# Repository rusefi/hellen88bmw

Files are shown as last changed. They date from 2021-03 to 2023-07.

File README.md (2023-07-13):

# Team

Product Owner @StefanSt

[Issue Tracker](https://github.com/rusefi/hellen88bmw-issues)

[User documentation](https://rusefi.com/s/hellen88bmw)

Part of https://github.com/andreika-git/hellen-one family

Inspired by https://github.com/rusefi/hw_88_bmw

# compatible cases

0260002360 TCU yes or no?

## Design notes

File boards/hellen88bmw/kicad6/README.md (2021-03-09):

Part of https://github.com/andreika-git/hellen-one family

https://docs.google.com/spreadsheets/d/1OiEaak7TElKwF-fXWvl9Dk-fD84a0NENe6lOwhXiOe4/

Inspired by https://github.com/rusefi/hw_88_bmw

https://github.com/rusefi/hw_microRusEfi

We shall start from https://github.com/rusefi/hellen121vag but using https://github.com/rusefi/hw_88_bmw shape and pinout.

Plan:

1) merge https://github.com/rusefi/hellen121vag MCU stuff with shape of https://github.com/rusefi/hw_88_bmw

from https://github.com/rusefi/hw_88_bmw we keep
   1) outline
   2) ignition coil drivers (we actually add two more - hw_88_bmw was a 6 cylinder board, we make a 8 cylinder ECU)
   3) MAP sensor position
   4) keep SD card somewhere
   5) 88 jumpers

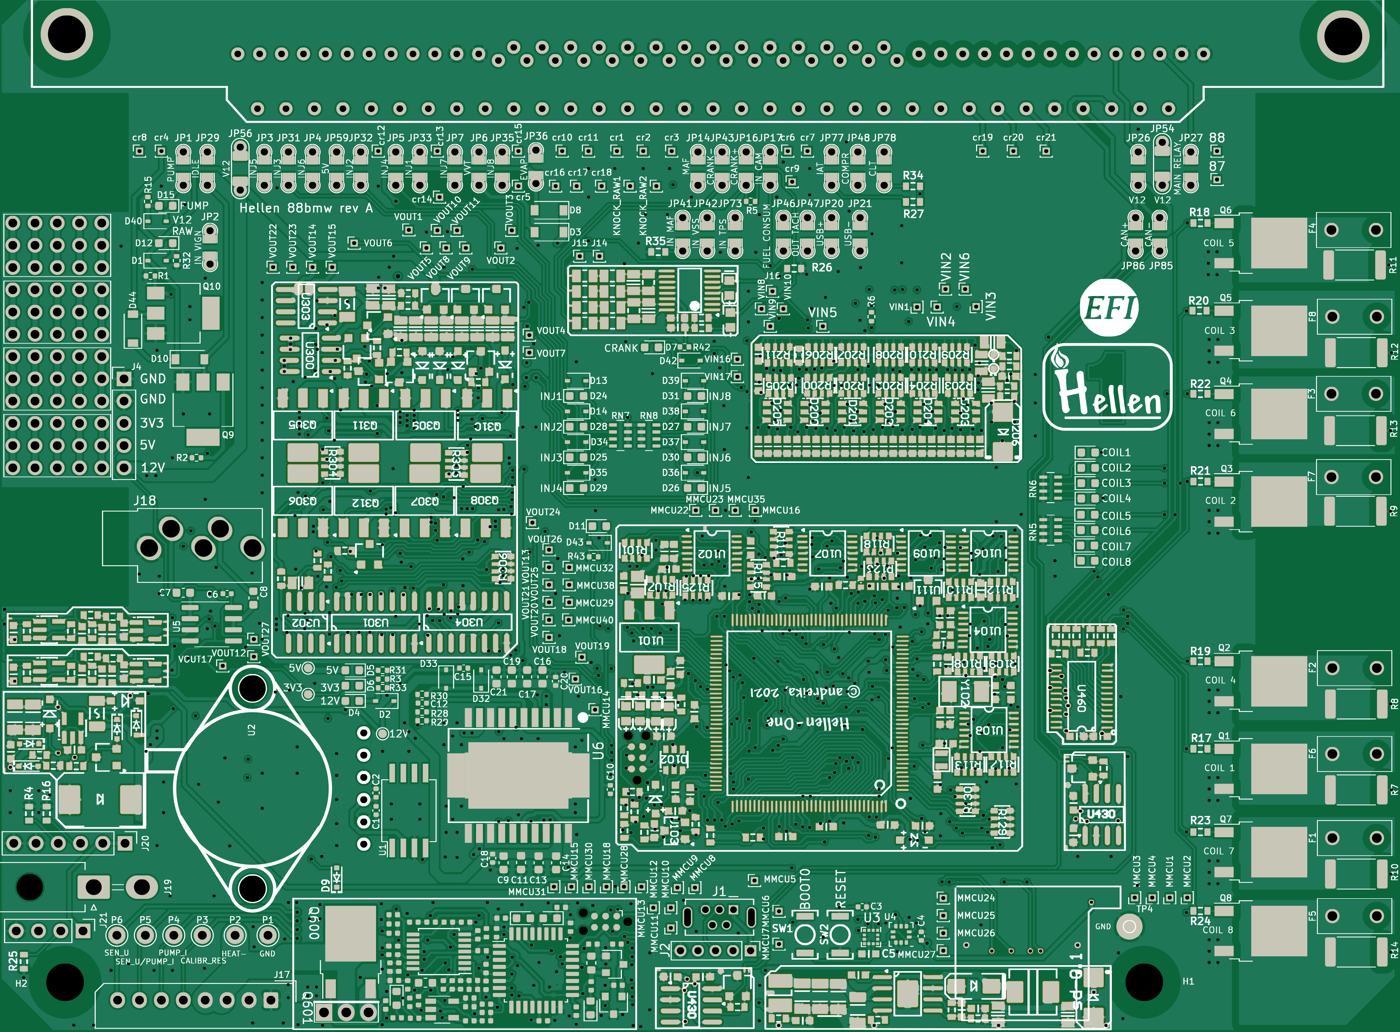
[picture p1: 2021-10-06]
boards/hellen88bmw-a/board/misc/hellen88bmw-a-top.png

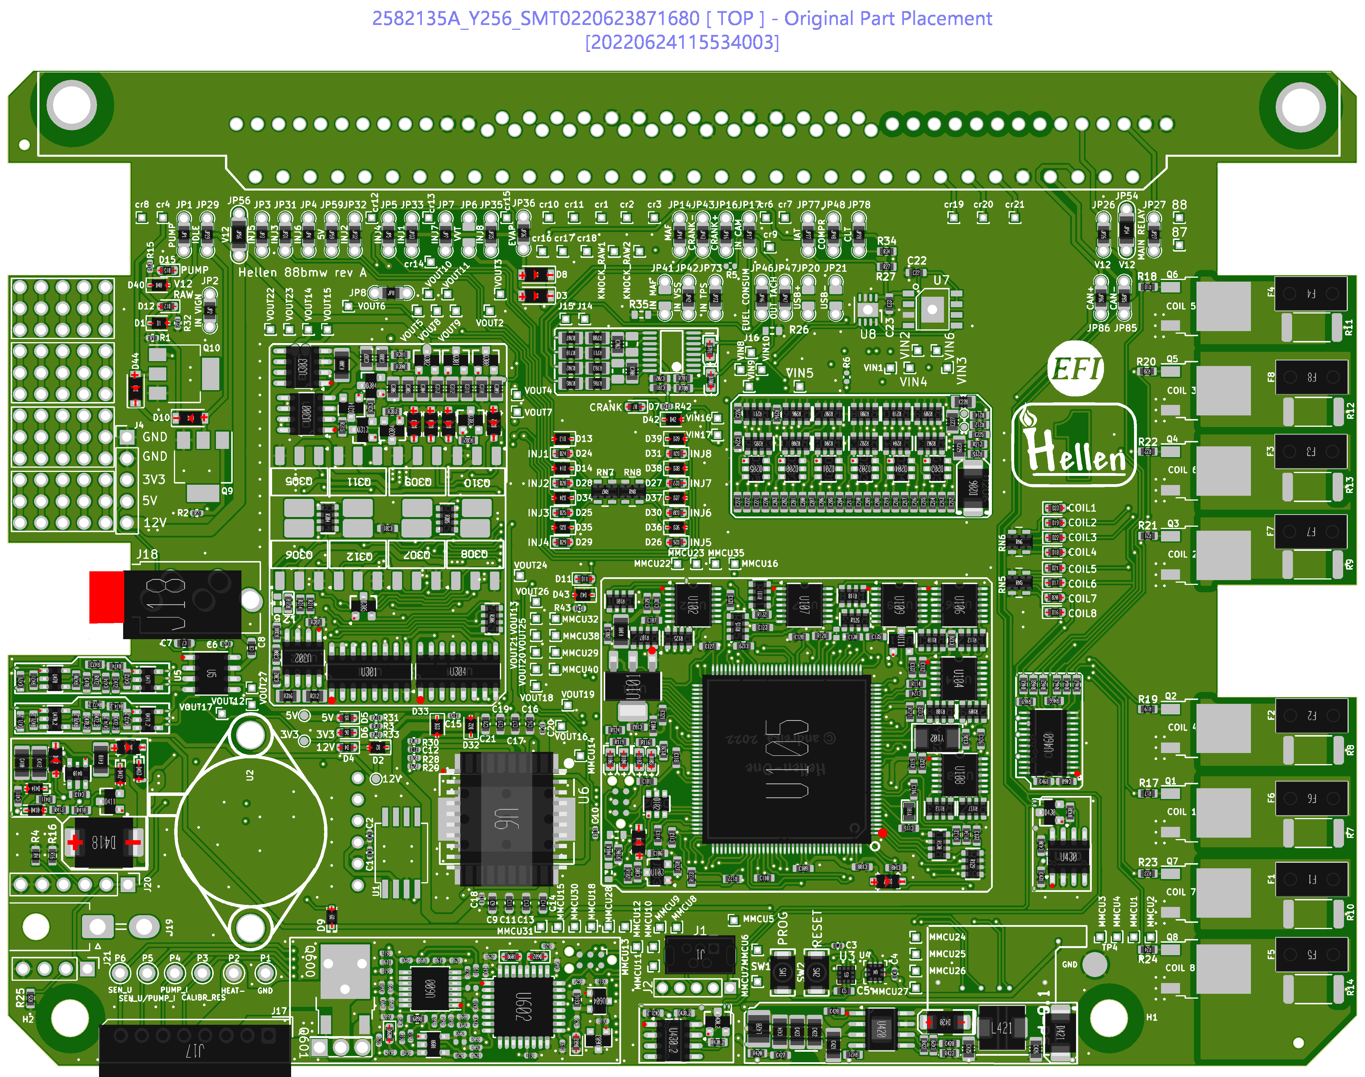
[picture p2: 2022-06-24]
boards/hellen88bmw-b/board/Produce_DanZhi.SMT_Original_Snapshot.Top.2582135A_Y256.SMT0220623871680.png

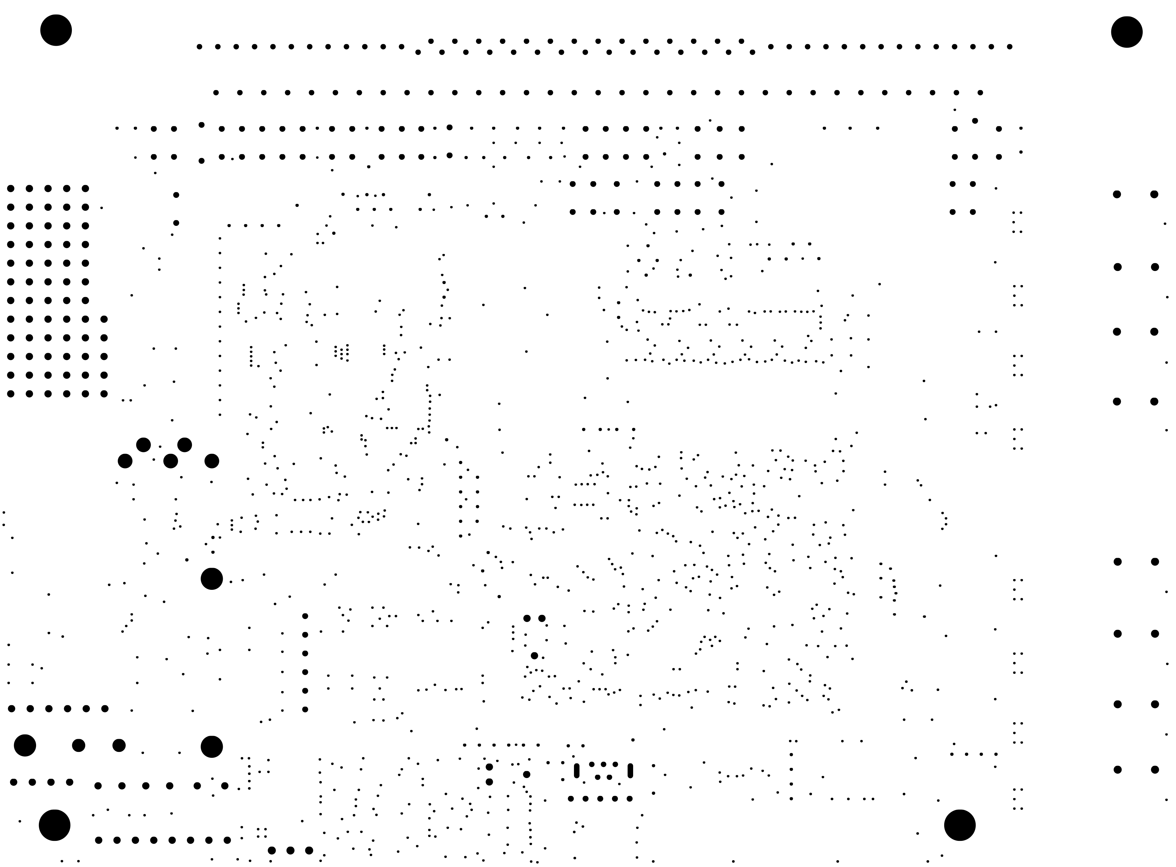
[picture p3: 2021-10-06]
boards/hellen88bmw-a/board/misc/hellen88bmw-a-outline.png

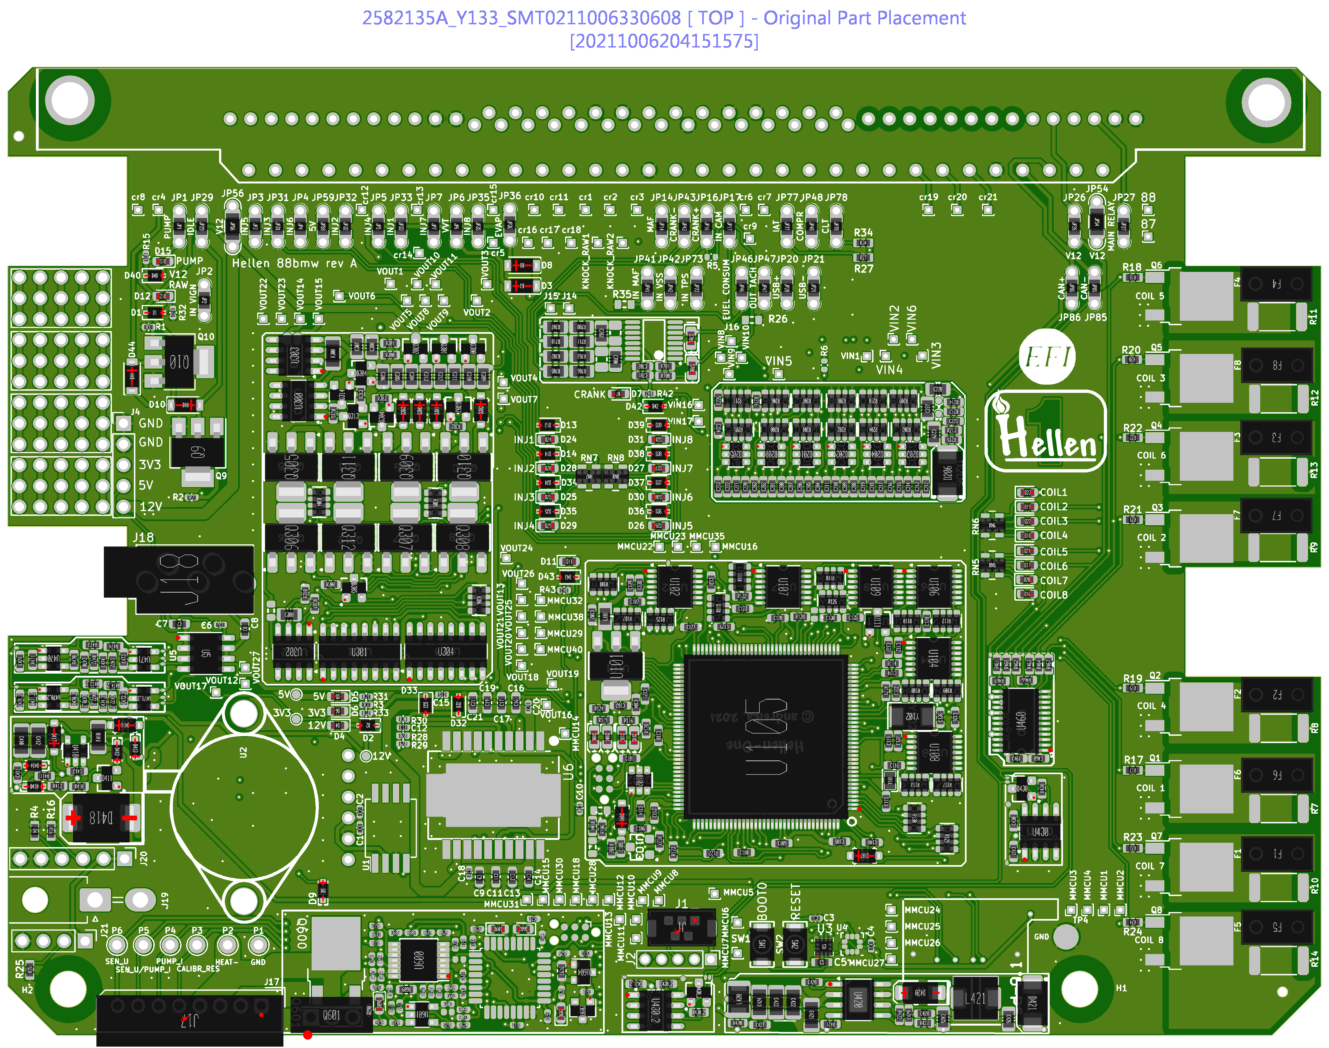
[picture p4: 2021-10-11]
boards/hellen88bmw-a/board/Produce_DanZhi.SMT_Original_Snapshot.Top.2582135A_Y133.SMT0211006330608.png

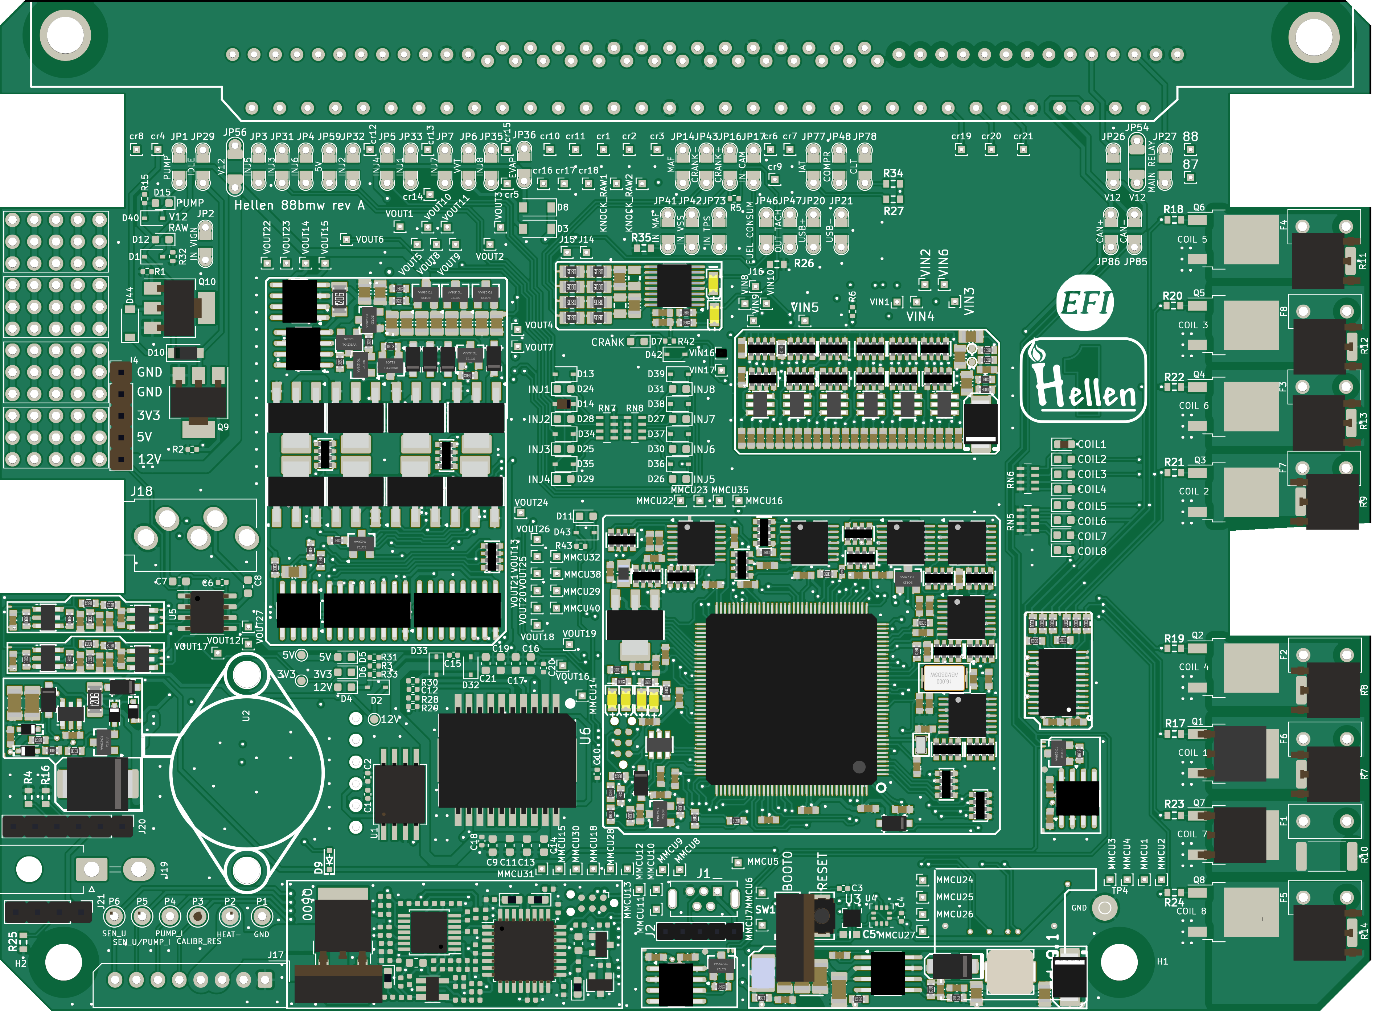
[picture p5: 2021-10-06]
boards/hellen88bmw-a/board/hellen88bmw-a.png

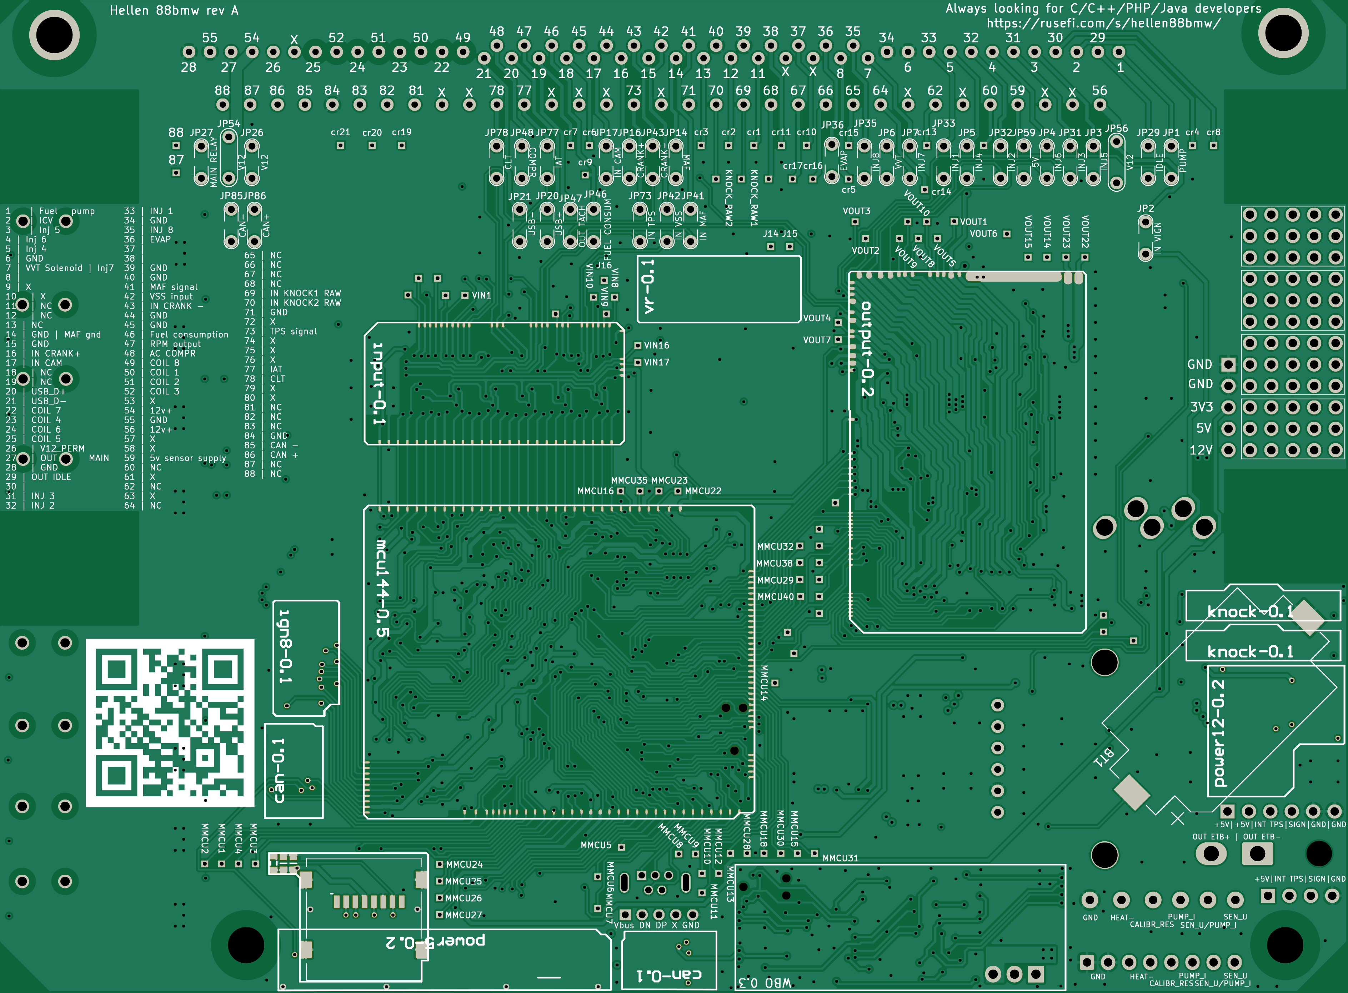
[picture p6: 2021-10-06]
boards/hellen88bmw-a/board/misc/hellen88bmw-a-bottom.png

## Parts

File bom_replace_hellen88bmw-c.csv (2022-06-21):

# remove the jumper connection from VCC_PP1 to +5V: we need +12v power supply for push-pull outputs.
R309
# remove +5V pull-ups from SPI1 | because we use it with +3.3v accelerometer
R103
R105
# remove jumper resistor connecting BOOT1 with A22 input line | because we use STM32F4
R131
# STM32
U105 | STM32F427ZGT6 | LQFP144 | C117816
#fuses
F410 | nSMD050-24V | F1206 | C70076
F300 | nSMD050-24V | F1206 | C70076
JP54 | Fuse-5A-1206 | F1206 | C553924
JP56 | Fuse-5A-1206 | F1206 | C553924
F101 | nSMD035-16V | SMD1206 | C70072
#pressure sensor
U4 | LPS22HBTR | HLGA-10L | C94049
#accelerometer
U3 | LIS2DH12TR | LGA-12 | C110926
#ETB driver
U6 | L6205PD | POWERSO20 | C1523898
#power distribution
U103 | AP2331W-7 | SOT-23 | C460346
# DC-DC Inductor
L421 | MWSA0503S-100MT | SMD-5.2x5.4x2.8 | C408412
#non-JLC components
#INJ low-side
Q305
Q306
Q307
Q308
Q309
Q310
Q311
Q312
Q9
Q10
#IGBT
Q1
Q2
Q3
Q4
Q5
Q6
Q7
Q8
#WBO low-side
Q600
Q601
#TLS115
U7
#MAX9926
U700
#include board_id_88bmw-b.csv

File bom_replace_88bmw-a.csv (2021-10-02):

# remove the jumper connection from VCC_PP1 to +5V: we need +12v power supply for push-pull outputs.
R309,
# remove +5V pull-ups from SPI1, because we use it with +3.3v accelerometer
R103,
R105,
# remove jumper resistor connecting BOOT1 with A22 input line, because we use STM32F4
R131,
# STM32
U105,"STM32F407ZGT7","LQFP144","C1337111"
# clock crystal
Y101,"SC-20S,32.768kHz,20PPM,7pF","2012","C97602"
# LMR14020->LMR14030 (more power, no problem)
U420,"LMR14030","SOP8","C182078"
#Vbat LDO
U410,"LP2981-33DBVR","SOT-23-5","C129997"
#power distribution
U103,"AP2331W-7","SOT-23","C460346"
U480,"AP2331W-7","SOT-23","C460346"
# DC-DC Inductor
L421,"MWSA0503S-100MT","SMD-5.2x5.4x2.8","C408412"
L420,"LBC3225T2R2MR","1210","C223413"
#accelerometer
U3,"LIS2DH12TR","LGA-12","C110926"
#INJ low-side
Q305,"ZXMS6005SGTA","SOT-223","C174042"
Q306,"ZXMS6005SGTA","SOT-223","C174042"
Q307,"ZXMS6005SGTA","SOT-223","C174042"
Q308,"ZXMS6005SGTA","SOT-223","C174042"
Q309,"ZXMS6005SGTA","SOT-223","C174042"
Q310,"ZXMS6005SGTA","SOT-223","C174042"
Q311,"ZXMS6005SGTA","SOT-223","C174042"
Q312,"ZXMS6005SGTA","SOT-223","C174042"
Q9,"ZXMS6005SGTA","SOT-223","C174042"
Q10,"ZXMS6005SGTA","SOT-223","C174042"
#non-JLC components
#pressure sensor
U4,
#IGBT
Q1,
Q2,
Q3,
Q4,
Q5,
Q6,
Q7,
Q8,
#ETB driver
U6,
#WBO low-side
Q600,
#WBO STM32
U602,

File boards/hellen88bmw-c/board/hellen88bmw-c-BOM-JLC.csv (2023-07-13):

Comment | Designator | Footprint | LCSC Part #
BATTERY_CR2032 | BT1 | BATTERY-2032 | C70377
100nF | C1, C2, C3, C4, C6, C18, C20 | C0402 | C307331
100n | C5, C411, C413, C430, C431, C430_2, C431_2, C420, C702, C204, C205, C206, C207, C212, C213, C214, C215, C220, C221, C222, C223, C224, C225, C226, C470, C460, C461, C101, C105, C106, C107, C108, C109, C110, C112, C113, C118, C119, C120, C121, C122, C123, C124, C126, C127, C128, C129, C130, C135, C139, C470_2 | C0603 | C14663
10u | C7, C8, C9, C11, C13, C14, C16, C17, C19, C21, C300 | C0603 | C96446
5.6nF | C10 | C0402 | C115688
10nF | C12 | C0402 | C15195
220nF | C15 | C0402 | C16772
1u | C22, C23, C133 | C0603 | C15849
1N4148WS | D1, D2, D9, D13, D14, D32, D33, D34, D35, D36, D37, D38, D39, D40, D42, D43, D410, D412, D413, D414 | SOD-323 | C2128
B5819W | D3, D8, D10, D44, D416, D417, D300, D301, D302, D303, D101, D107 | SOD-123 | C8598
LED-GREEN-0603 | D4, D5, D6, D12, D601, D104 | LED-0603 | C72043
LED-WHITE-0603 | D7 | LED-0603 | C84265
LED-RED-0603 | D11, D15, D24, D25, D26, D27, D28, D29, D30, D31, D600, D603, D700, D701, D103 | LED-0603 | C2286
LED-BLUE-0603 | D16, D17, D18, D19, D20, D21, D22, D23, D602, D105 | LED-0603 | C72041
10A | F1, F2, F3, F4, F5, F6, F7, F8 | 36911600000 | C354908
USB_B_Mini | J1 | USB-MINI-B-VERTICAL | C13453
XH-8A | J17 | XH-8A | C10385
AudioJack_THR | J18 | Jack_3.5mm_PJ-3250-5A | C165947
Jumper_2_Open | JP1, JP2, JP3, JP4, JP5, JP7, JP8, JP14, JP16, JP17, JP26, JP27, JP29, JP31, JP32, JP33, JP35, JP36, JP42, JP43, JP46, JP47, JP48, JP59, JP73, JP77, JP78, JP85, JP86 | PAD-0805-PAD | C17477
10k | R1, R2, R29 | R0402 | C60489
750R | R3 | R0402 | C25132
680k | R4, R16, R25 | R0603 | C25822
DNP | R7, R8, R9, R10, R11, R12, R13, R14 | R2512 | NA
20k | R15, R610, R611, R612 | R0402 | C25765
22 | R17, R18, R19, R20, R21, R22, R23, R24 | R0603 | C23345
2.7k | R27, R34 | R0603 | C13167
100k | R28 | R0402 | C106234
100 | R30 | R0402 | C106233
1k6 | R31 | R0402 | C25931
5k1 | R32, R33, R43 | R0402 | C25941
4.7k | R42 | R0402 | C25940
1k | RN5, RN6 | R_Array_Concave_4x0603 | C240722
4.7k | RN7, RN8, R200, R201, R202, R203, R204, R205, R207 | R0603-4 | C1980
Button_SPST | SW1, SW2 | SMD-2_2.9x3.9x1.7 | C115357
MCP6002-xSN | U5 | SO8 | C7377
47u | C410, C412 | C1206 | C96123
PSM712-LF | D411, D304, D305 | SOT-23 | C32677
SMCJ30A | D418 | SMC | C310046
6.8k | R410, R413 | R0603 | C23212
33k | R411, R474, R474_2, R450 | R0603 | C4216
MIC5205-3.3YM5 | U410 | SOT23-5 | C37970
PESD1CAN | D430, D430_2 | SOT-23 | C343993
120 | R430, R430_2 | R0603 | C22787
TJA1051T/3/1J | U430, U430_2 | SO8 | C38695
1u | C600, C607, C609, C610, C611 | C0402 | C52923
100n | C601, C602, C605, C608, C612, C613, C614, C615 | C0402 | C1525
33n | C603 | C0402 | C1585
4.7u | C616, C427, C102, C103, C104, C137, C138, C140 | C0603 | C19666
1k | R600, R601, R616, R617, R622, R626, R627, R628 | R0402 | C11702
68k | R602, R603 | R0402 | C36871
10k | R604, R605, R613, R614, R618, R619, R625 | R0402 | C25744
10 | R606 | R0402 | C25077
22k | R607 | R0402 | C25768
47 | R608 | R0402 | C25118
61.9 | R609 | R0603 | C23092
100k | R615, R621 | R0402 | C25741
27k | R620, R623 | R0402 | C25771
3.3k | R624 | R0402 | C25890
MCP6004 | U600, U102, U104, U106, U107, U108, U109 | TSSOP14 | C50282
AD8628 | U601 | TSOT23-5 | C29309
STM32F042K6Tx | U602 | LQFP32 | C69216
REF3033 | U603 | SOT-23 | C36658
XC6206P332MR | U604, U111 | SOT-23 | C5446
10u | C421, C422, C423, C424 | C1206 | C13585
10u | C425, C426, C304, C305, C306, C307, C308, C309, C310, C311, C312, C313 | C0805 | C15850
10n | C428, C201, C208, C209, C210, C211, C301, C302 | C0603 | C57112
220p | C429 | C0603 | C1603
SS34 | D420 | SMA | C8678
P6SMB6.8CA | D421, D206 | SMB | C78395
2.2uH | L420 | L1210 | C36828
1 | R420 | R0603 | C22936
10k | R421, R700, R701, R300, R301, R307, R308, R315, R102, R121, R127, R128 | R0603 | C25804
68k | R422 | R0603 | C23231
12k | R423, R472, R472_2 | R0603 | C22790
LMR14020 | U420 | SOP8 | C187824
1n | C700, C703 | C0805 | C46653
10u | C701 | C0603 | C19702
5.1k | R702, R703, R705, R706, R707, R708, R710, R711 | R0805 | C27834
1n | C200, C202, C203, C216, C217, C218, C219 | C0603 | C1588
2.2u | C227, C228, C229 | C0805 | C49217
SRV05-4-P-T7 | D200, D201, D202, D203, D204, D205, D102 | SOT23-6 | C85364
680k | R206, R209, R211 | R0603-4 | C145776
10k | R208, R210, R304, R305, R306, R129, R130 | R0603-4 | C29718
510 | R212, R213, R214, R215, R116, R119, R120, R124 | R0603 | C23193
3.3k | R216 | R0603 | C22978
3.3n | C471, C471_2 | C0603 | C1613
330p | C472, C472_2 | C0603 | C1664
47p | C473, C473_2 | C0603 | C1671
680p | C474, C474_2 | C0603 | C1630
470k | R470, R470_2 | R0603 | C23178
100k | R471, R473, R471_2, R473_2 | R0603 | C25803
LMV321IDBVR | U470, U471, U470_2, U471_2 | SOT23-5 | C7972
PJM2319PSA | Q300, Q301, Q302, Q303, Q304, Q313, Q314 | SOT-23 | C411720
4.7k | R302, R303, R313 | R0603 | C23162
0 | R310 | R0603 | C21189
1k | R311, R314 | R0603 | C21190
100 | R312, R316 | R0805 | C17408
RZ7899 | U300, U303 | SO8 | C92373
ULN2003AD | U301, U304 | SOIC16 | C7512
TC4427 | U302 | SO8 | C20551
10 | R461, R462, R463, R464, R466, R467, R468, R469 | R0603 | C22859
SN74LVC4245APWR | U460 | TSSOP24 | C7859
2.2u | C114, C131 | C0603 | C23630
12p | C115, C116 | C0603 | C38523
18p | C132, C136 | C0603 | C1647
LED-YELLOW-0603 | D106 | LED-0603 | C72038
4.7k | R101, R107, R108, R109, R110, R111, R112, R113, R115, R117, R118, R125, R126 | R0603-4 | C66697
100 | R104, R106 | R0603 | C22775
47 | R114 | R0603 | C23182
2.2k | R122, R123 | R0603 | C4190
5.1k | R132 | R0603 | C23186
AMS1117-3.3 | U101 | SOT-223 | C6186
32.768 kHz | Y101 | SMD2012 | C99009
20 MHz | Y102 | SMD5032 | C112566
22u | C450, C451 | C0603 | C59461
Molex MicroSD 47219-2001 | J450 | SDAMB-012 | C164170
STM32F427ZGT6 | U105 | LQFP144 | C117816
nSMD050-24V | F410, F300 | F1206 | C70076
Fuse-5A-1206 | JP54, JP56 | F1206 | C553924
nSMD035-16V | F101 | SMD1206 | C70072
LPS22HBTR | U4 | HLGA-10L | C94049
LIS2DH12TR | U3 | LGA-12 | C110926
L6205PD | U6 | POWERSO20 | C1523898
AP2331W-7 | U103 | SOT-23 | C460346
MWSA0503S-100MT | L421 | SMD-5.2x5.4x2.8 | C408412
620 | R133, R134 | R0603 | C23220

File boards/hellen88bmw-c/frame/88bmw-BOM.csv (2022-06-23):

Comment | Designator | Footprint | LCSC Part #
BATTERY_CR2032 | BT1 | BATTERY-2032 | C70377
100nF | C1 | C0402 | C307331
100nF | C2 | C0402 | C307331
100nF | C3 | C0402 | C307331
100nF | C4 | C0402 | C307331
100n | C5 | C0603 | C14663
100nF | C6 | C0402 | C307331
10u | C7 | C0603 | C96446
10u | C8 | C0603 | C96446
10u | C9 | C0603 | C96446
5.6nF | C10 | C0402 | C115688
10u | C11 | C0603 | C96446
10nF | C12 | C0402 | C15195
10u | C13 | C0603 | C96446
10u | C14 | C0603 | C96446
220nF | C15 | C0402 | C16772
10u | C16 | C0603 | C96446
10u | C17 | C0603 | C96446
100nF | C18 | C0402 | C307331
10u | C19 | C0603 | C96446
100nF | C20 | C0402 | C307331
10u | C21 | C0603 | C96446
1u | C22 | C0603 | C15849
1u | C23 | C0603 | C15849
cr | cr1 | PinHeader_1x01_P1.00mm_Vertical
cr | cr2 | PinHeader_1x01_P1.00mm_Vertical
cr | cr3 | PinHeader_1x01_P1.00mm_Vertical
cr | cr4 | PinHeader_1x01_P1.00mm_Vertical
cr | cr6 | PinHeader_1x01_P1.00mm_Vertical
cr | cr7 | PinHeader_1x01_P1.00mm_Vertical
cr | cr8 | PinHeader_1x01_P1.00mm_Vertical
cr | cr9 | PinHeader_1x01_P1.00mm_Vertical
cr | cr10 | PinHeader_1x01_P1.00mm_Vertical
cr | cr11 | PinHeader_1x01_P1.00mm_Vertical
cr | cr12 | PinHeader_1x01_P1.00mm_Vertical
cr | cr13 | PinHeader_1x01_P1.00mm_Vertical
cr | cr14 | PinHeader_1x01_P1.00mm_Vertical
cr | cr15 | PinHeader_1x01_P1.00mm_Vertical
cr | cr16 | PinHeader_1x01_P1.00mm_Vertical
cr | cr17 | PinHeader_1x01_P1.00mm_Vertical
cr | cr18 | PinHeader_1x01_P1.00mm_Vertical
cr | cr19 | PinHeader_1x01_P1.00mm_Vertical
cr | cr20 | PinHeader_1x01_P1.00mm_Vertical
cr | cr21 | PinHeader_1x01_P1.00mm_Vertical
cr | cr22 | PinHeader_1x01_P1.00mm_Vertical
cr | cr23 | PinHeader_1x01_P1.00mm_Vertical
1N4148WS | D1 | D_SOD-323 | C2128
1N4148WS | D2 | D_SOD-323 | C2128
B5819W | D3 | D_SOD-123 | C8598
LED-GREEN-0603 | D4 | LED-0603 | C72043
LED-GREEN-0603 | D5 | LED-0603 | C72043
LED-GREEN-0603 | D6 | LED-0603 | C72043
LED-WHITE-0603 | D7 | LED-0603 | C84265
B5819W | D8 | D_SOD-123 | C8598
1N4148WS | D9 | SOD-323 | C2128
B5819W | D10 | D_SOD-123 | C8598
LED-RED-0603 | D11 | LED-0603 | C2286
LED-GREEN-0603 | D12 | LED-0603 | C72043
1N4148WS | D13 | D_SOD-323 | C2128
1N4148WS | D14 | D_SOD-323 | C2128
LED-RED-0603 | D15 | LED-0603 | C2286
LED-BLUE-0603 | D16 | LED-0603 | C72041
LED-BLUE-0603 | D17 | LED-0603 | C72041
LED-BLUE-0603 | D18 | LED-0603 | C72041
LED-BLUE-0603 | D19 | LED-0603 | C72041
LED-BLUE-0603 | D20 | LED-0603 | C72041
LED-BLUE-0603 | D21 | LED-0603 | C72041
LED-BLUE-0603 | D22 | LED-0603 | C72041
LED-BLUE-0603 | D23 | LED-0603 | C72041
LED-RED-0603 | D24 | LED-0603 | C2286
LED-RED-0603 | D25 | LED-0603 | C2286
LED-RED-0603 | D26 | LED-0603 | C2286
LED-RED-0603 | D27 | LED-0603 | C2286
LED-RED-0603 | D28 | LED-0603 | C2286
LED-RED-0603 | D29 | LED-0603 | C2286
LED-RED-0603 | D30 | LED-0603 | C2286
LED-RED-0603 | D31 | LED-0603 | C2286
1N4148WS | D32 | D_SOD-323 | C2128
1N4148WS | D33 | D_SOD-323 | C2128
1N4148WS | D34 | D_SOD-323 | C2128
1N4148WS | D35 | D_SOD-323 | C2128
1N4148WS | D36 | D_SOD-323 | C2128
1N4148WS | D37 | D_SOD-323 | C2128
1N4148WS | D38 | D_SOD-323 | C2128
1N4148WS | D39 | D_SOD-323 | C2128
1N4148WS | D40 | D_SOD-323 | C2128
1N4148WS | D42 | D_SOD-323 | C2128
1N4148WS | D43 | D_SOD-323 | C2128
B5819W | D44 | D_SOD-123 | C8598
10A | F1 | 36911600000 | C354908
10A | F2 | 36911600000 | C354908
10A | F3 | 36911600000 | C354908
10A | F4 | 36911600000 | C354908
10A | F5 | 36911600000 | C354908
10A | F6 | 36911600000 | C354908
10A | F7 | 36911600000 | C354908
10A | F8 | 36911600000 | C354908
LOGO | G1 | LOGO
LOGO | G2 | LOGO
PROTO_AREA | G3 | PROTO_AREA
PROTO_AREA | G4 | PROTO_AREA
PROTO_AREA | G6 | PROTO_AREA
PROTO_AREA | G7 | PROTO_AREA
MountingHole | H1 | MountingHole_4.3mm_M4_DIN965
MountingHole | H2 | MountingHole_4.3mm_M4_DIN965
USB_B_Mini | J1 | USB-MINI-B-VERTICAL | C13453
Conn_01x05 | J2 | PinHeader_1x05_P2.00mm_Vertical
Conn_01x05 | J4 | PinHeader_1x05_P2.54mm_Vertical
VRIN1 | J14 | PinHeader_1x01_P1.00mm_Vertical
VRIN2 | J15 | PinHeader_1x01_P1.00mm_Vertical
VROUT1 | J16 | PinHeader_1x01_P1.00mm_Vertical
XH-8A | J17 | XH-8A | C10385
AudioJack_THR | J18 | Jack_3.5mm_PJ-3250-5A | C165947
MiniFit | J19 | Molex_Mini-Fit_Jr_5569-02A2_2x01_P4.20mm_Horizontal
ETB | J20 | PinHeader_1x06_P2.54mm_Vertical
PPS | J21 | PinHeader_1x04_P2.54mm_Vertical
Jumper_2_Open | JP1 | PAD-0805-PAD | C17477
Jumper_2_Open | JP2 | PAD-0805-PAD | C17477
Jumper_2_Open | JP3 | PAD-0805-PAD | C17477
Jumper_2_Open | JP4 | PAD-0805-PAD | C17477
Jumper_2_Open | JP5 | PAD-0805-PAD | C17477
Jumper_2_Open | JP6 | PAD-0805-PAD
Jumper_2_Open | JP7 | PAD-0805-PAD | C17477
Jumper_2_Open | JP8 | PAD-0805-PAD | C17477
Jumper_2_Open | JP14 | PAD-0805-PAD | C17477
Jumper_2_Open | JP16 | PAD-0805-PAD | C17477
Jumper_2_Open | JP17 | PAD-0805-PAD | C17477
Jumper_2_Open | JP20 | PAD-0805-PAD
Jumper_2_Open | JP21 | PAD-0805-PAD
Jumper_2_Open | JP26 | PAD-0805-PAD | C17477
Jumper_2_Open | JP27 | PAD-0805-PAD | C17477
Jumper_2_Open | JP29 | PAD-0805-PAD | C17477
Jumper_2_Open | JP31 | PAD-0805-PAD | C17477
Jumper_2_Open | JP32 | PAD-0805-PAD | C17477
Jumper_2_Open | JP33 | PAD-0805-PAD | C17477
Jumper_2_Open | JP35 | PAD-0805-PAD | C17477
Jumper_2_Open | JP36 | PAD-0805-PAD | C17477
Jumper_2_Open | JP41 | PAD-0805-PAD
Jumper_2_Open | JP42 | PAD-0805-PAD | C17477
Jumper_2_Open | JP43 | PAD-0805-PAD | C17477
Jumper_2_Open | JP46 | PAD-0805-PAD | C17477
Jumper_2_Open | JP47 | PAD-0805-PAD | C17477
Jumper_2_Open | JP48 | PAD-0805-PAD | C17477
Jumper_2_Open | JP54 | PAD-1206-PAD | C182446
Jumper_2_Open | JP56 | PAD-1206-PAD | C182446
Jumper_2_Open | JP59 | PAD-0805-PAD | C17477
Jumper_2_Open | JP73 | PAD-0805-PAD | C17477
Jumper_2_Open | JP77 | PAD-0805-PAD | C17477
Jumper_2_Open | JP78 | PAD-0805-PAD | C17477
Jumper_2_Open | JP85 | PAD-0805-PAD | C17477
Jumper_2_Open | JP86 | PAD-0805-PAD | C17477
IN_KNOCK1_RAW | KNOCK_RAW1 | PinHeader_1x01_P1.00mm_Vertical
IN_KNOCK2_RAW | KNOCK_RAW2 | PinHeader_1x01_P1.00mm_Vertical
Module:power12/0.2 | M1 | power12
Module:can/0.1 | M2 | can
Module:wbo/0.3 | M3 | wbo
Module:can/0.1 | M4 | can
Module:power5/0.2 | M5 | power5
Module:vr/0.1 | M6 | vr
Module:input/0.1 | M7 | input
Module:knock/0.1 | M8 | knock
Module:output/0.3 | M9 | output
Module:ign8/0.2 | M10 | ign8
Module:mcu144/0.6 | M11 | mcu
Module:knock/0.1 | M12 | knock
Module:sd/0.1 | M13 | sd
MMCU | MMCU1 | PinHeader_1x01_P1.00mm_Vertical
MMCU | MMCU2 | PinHeader_1x01_P1.00mm_Vertical
MMCU | MMCU3 | PinHeader_1x01_P1.00mm_Vertical
MMCU | MMCU4 | PinHeader_1x01_P1.00mm_Vertical
MMCU | MMCU5 | PinHeader_1x01_P1.00mm_Vertical
MMCU | MMCU6 | PinHeader_1x01_P1.00mm_Vertical
MMCU | MMCU7 | PinHeader_1x01_P1.00mm_Vertical
MMCU | MMCU8 | PinHeader_1x01_P1.00mm_Vertical
MMCU | MMCU9 | PinHeader_1x01_P1.00mm_Vertical
MMCU | MMCU10 | PinHeader_1x01_P1.00mm_Vertical
MMCU | MMCU11 | PinHeader_1x01_P1.00mm_Vertical
MMCU | MMCU12 | PinHeader_1x01_P1.00mm_Vertical
MMCU | MMCU13 | PinHeader_1x01_P1.00mm_Vertical
MMCU | MMCU14 | PinHeader_1x01_P1.00mm_Vertical
MMCU | MMCU15 | PinHeader_1x01_P1.00mm_Vertical
MMCU | MMCU16 | PinHeader_1x01_P1.00mm_Vertical
MMCU | MMCU18 | PinHeader_1x01_P1.00mm_Vertical
MMCU | MMCU22 | PinHeader_1x01_P1.00mm_Vertical
MMCU | MMCU23 | PinHeader_1x01_P1.00mm_Vertical
MMCU | MMCU24 | PinHeader_1x01_P1.00mm_Vertical
MMCU | MMCU25 | PinHeader_1x01_P1.00mm_Vertical
MMCU | MMCU26 | PinHeader_1x01_P1.00mm_Vertical
MMCU | MMCU27 | PinHeader_1x01_P1.00mm_Vertical
MMCU | MMCU28 | PinHeader_1x01_P1.00mm_Vertical
MMCU | MMCU29 | PinHeader_1x01_P1.00mm_Vertical
MMCU | MMCU30 | PinHeader_1x01_P1.00mm_Vertical
MMCU | MMCU31 | PinHeader_1x01_P1.00mm_Vertical
MMCU | MMCU32 | PinHeader_1x01_P1.00mm_Vertical
MMCU | MMCU35 | PinHeader_1x01_P1.00mm_Vertical
MMCU | MMCU38 | PinHeader_1x01_P1.00mm_Vertical
MMCU | MMCU40 | PinHeader_1x01_P1.00mm_Vertical
P | P1 | Pin_D1.0mm_L10.0mm
P | P2 | Pin_D1.0mm_L10.0mm
P | P3 | Pin_D1.0mm_L10.0mm
P | P4 | Pin_D1.0mm_L10.0mm
P | P5 | Pin_D1.0mm_L10.0mm
P | P6 | Pin_D1.0mm_L10.0mm
Motronic_88pin | PP1 | 88pin_STS
NGD8201AN | Q1 | DPAK | C151649
NGD8201AN | Q2 | DPAK | C151649
NGD8201AN | Q3 | DPAK | C151649
NGD8201AN | Q4 | DPAK | C151649
NGD8201AN | Q5 | DPAK | C151649
NGD8201AN | Q6 | DPAK | C151649
NGD8201AN | Q7 | DPAK | C151649
NGD8201AN | Q8 | DPAK | C151649
AUIPS2041LTR | Q9 | SOT-223 | C113610
AUIPS2041LTR | Q10 | SOT-223 | C113610
10k | R1 | R0402 | C60489
10k | R2 | R0402 | C60489
750R | R3 | R0402 | C25132
680k | R4 | R0603 | C25822
DNP | R5 | R0402
DNP | R6 | R0402
DNP | R7 | R2512 | NA
DNP | R8 | R2512 | NA
DNP | R9 | R2512 | NA
DNP | R10 | R2512 | NA
DNP | R11 | R2512 | NA
DNP | R12 | R2512 | NA
DNP | R13 | R2512 | NA
DNP | R14 | R2512 | NA
20k | R15 | R0402 | C25765
680k | R16 | R0603 | C25822
22 | R17 | R0603 | C23345
22 | R18 | R0603 | C23345
22 | R19 | R0603 | C23345
22 | R20 | R0603 | C23345
22 | R21 | R0603 | C23345
22 | R22 | R0603 | C23345
22 | R23 | R0603 | C23345
22 | R24 | R0603 | C23345
680k | R25 | R0603 | C25822
DNP | R26 | R0603
2.7k | R27 | R0603 | C13167
100k | R28 | R0402 | C106234
10k | R29 | R0402 | C60489
100 | R30 | R0402 | C106233
1k6 | R31 | R0402 | C25931
5k1 | R32 | R0402 | C25941
5k1 | R33 | R0402 | C25941
2.7k | R34 | R0603 | C13167
DNP | R35 | R0603
4.7k | R42 | R0402 | C25940
5k1 | R43 | R0402 | C25941
1k | RN5 | R_Array_Concave_4x0603 | C240722
1k | RN6 | R_Array_Concave_4x0603 | C240722
4.7k | RN7 | R_Array_Concave_4x0603 | C1980
4.7k | RN8 | R_Array_Concave_4x0603 | C1980
Button_SPST | SW1 | SMD-2_2.9x3.9x1.7 | C115357
Button_SPST | SW2 | SMD-2_2.9x3.9x1.7 | C115357
TestPoint | TP1 | TestPoint_Pad_D1.0mm
TestPoint | TP2 | TestPoint_Pad_D1.0mm
TestPoint | TP3 | TestPoint_Pad_D1.0mm
TestPoint | TP4 | TestPoint_Pad_D1.0mm
MPXA6115A | U1 | SSO-8_6.8x5.9mm_P1.27mm_Clearance7mm
MPX4_MAP | U2 | MPX-4_MAP
LIS2DW12TR | U3 | LGA-12_2x2mm_P0.5mm | C189624
LPS25HB | U4 | HLGA-10 | C87898
MCP6002-xSN | U5 | SO8 | C7377
L6205PD | U6 | SO20POWER | C36543
TLS115_SOIC | U7 | PG-DSO-8-43 | C540242
TLS115_SON | U8 | HVSON-8-1EP_3x3mm_P0.65mm_EP1.6x2.4mm
VIN8 | VIN1 | PinHeader_1x01_P1.00mm_Vertical
VIN8 | VIN2 | PinHeader_1x01_P1.00mm_Vertical
VIN8 | VIN3 | PinHeader_1x01_P1.00mm_Vertical
VIN8 | VIN4 | PinHeader_1x01_P1.00mm_Vertical
VIN8 | VIN5 | PinHeader_1x01_P1.00mm_Vertical
VIN8 | VIN6 | PinHeader_1x01_P1.00mm_Vertical
VIN8 | VIN8 | PinHeader_1x01_P1.00mm_Vertical
VIN9 | VIN9 | PinHeader_1x01_P1.00mm_Vertical
VIN10 | VIN10 | PinHeader_1x01_P1.00mm_Vertical
VIN16 | VIN16 | PinHeader_1x01_P1.00mm_Vertical
VIN17 | VIN17 | PinHeader_1x01_P1.00mm_Vertical
VOUT4 | VOUT2 | PinHeader_1x01_P1.00mm_Vertical
VOUT4 | VOUT3 | PinHeader_1x01_P1.00mm_Vertical
VOUT4 | VOUT4 | PinHeader_1x01_P1.00mm_Vertical
VOUT5 | VOUT5 | PinHeader_1x01_P1.00mm_Vertical
VOUT6 | VOUT6 | PinHeader_1x01_P1.00mm_Vertical
VOUT4 | VOUT7 | PinHeader_1x01_P1.00mm_Vertical
VOUT4 | VOUT8 | PinHeader_1x01_P1.00mm_Vertical
VOUT4 | VOUT9 | PinHeader_1x01_P1.00mm_Vertical
VOUT4 | VOUT10 | PinHeader_1x01_P1.00mm_Vertical
VOUT4 | VOUT11 | PinHeader_1x01_P1.00mm_Vertical
VOUT4 | VOUT12 | PinHeader_1x01_P1.00mm_Vertical
VOUT4 | VOUT13 | PinHeader_1x01_P1.00mm_Vertical
VOUT4 | VOUT14 | PinHeader_1x01_P1.00mm_Vertical
VOUT4 | VOUT15 | PinHeader_1x01_P1.00mm_Vertical
VOUT4 | VOUT16 | PinHeader_1x01_P1.00mm_Vertical
VOUT4 | VOUT17 | PinHeader_1x01_P1.00mm_Vertical
VOUT4 | VOUT18 | PinHeader_1x01_P1.00mm_Vertical
VOUT4 | VOUT19 | PinHeader_1x01_P1.00mm_Vertical
VOUT4 | VOUT20 | PinHeader_1x01_P1.00mm_Vertical
VOUT4 | VOUT21 | PinHeader_1x01_P1.00mm_Vertical
VOUT4 | VOUT22 | PinHeader_1x01_P1.00mm_Vertical
VOUT4 | VOUT23 | PinHeader_1x01_P1.00mm_Vertical
VOUT4 | VOUT24 | PinHeader_1x01_P1.00mm_Vertical
VOUT4 | VOUT25 | PinHeader_1x01_P1.00mm_Vertical
VOUT4 | VOUT26 | PinHeader_1x01_P1.00mm_Vertical
VOUT4 | VOUT27 | PinHeader_1x01_P1.00mm_Vertical

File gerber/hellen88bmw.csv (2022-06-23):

Comment | Designator | Footprint | LCSC Part #
BATTERY_CR2032 | BT1 | Battery:BatteryHolder_Keystone_1060_1x2032 | C70377
100nF | C1 | Capacitor_SMD:C_0402_1005Metric | C307331
100nF | C2 | Capacitor_SMD:C_0402_1005Metric | C307331
100nF | C3 | Capacitor_SMD:C_0402_1005Metric | C307331
100nF | C4 | Capacitor_SMD:C_0402_1005Metric | C307331
100n | C5 | hellen-one-common:C0603 | C14663
100nF | C6 | Capacitor_SMD:C_0402_1005Metric | C307331
10u | C7 | Capacitor_SMD:C_0603_1608Metric | C96446
10u | C8 | Capacitor_SMD:C_0603_1608Metric | C96446
10u | C9 | Capacitor_SMD:C_0603_1608Metric | C96446
5.6nF | C10 | Capacitor_SMD:C_0402_1005Metric | C115688
10u | C11 | Capacitor_SMD:C_0603_1608Metric | C96446
10nF | C12 | Capacitor_SMD:C_0402_1005Metric | C15195
10u | C13 | Capacitor_SMD:C_0603_1608Metric | C96446
10u | C14 | Capacitor_SMD:C_0603_1608Metric | C96446
220nF | C15 | Capacitor_SMD:C_0402_1005Metric | C16772
10u | C16 | Capacitor_SMD:C_0603_1608Metric | C96446
10u | C17 | Capacitor_SMD:C_0603_1608Metric | C96446
100nF | C18 | Capacitor_SMD:C_0402_1005Metric | C307331
10u | C19 | Capacitor_SMD:C_0603_1608Metric | C96446
100nF | C20 | Capacitor_SMD:C_0402_1005Metric | C307331
10u | C21 | Capacitor_SMD:C_0603_1608Metric | C96446
1u | C22 | hellen-one-common:C0603 | C15849
1u | C23 | hellen-one-common:C0603 | C15849
cr | cr1 | Connector_PinHeader_1.00mm:PinHeader_1x01_P1.00mm_Vertical
cr | cr2 | Connector_PinHeader_1.00mm:PinHeader_1x01_P1.00mm_Vertical
cr | cr3 | Connector_PinHeader_1.00mm:PinHeader_1x01_P1.00mm_Vertical
cr | cr4 | Connector_PinHeader_1.00mm:PinHeader_1x01_P1.00mm_Vertical
cr | cr6 | Connector_PinHeader_1.00mm:PinHeader_1x01_P1.00mm_Vertical
cr | cr7 | Connector_PinHeader_1.00mm:PinHeader_1x01_P1.00mm_Vertical
cr | cr8 | Connector_PinHeader_1.00mm:PinHeader_1x01_P1.00mm_Vertical
cr | cr9 | Connector_PinHeader_1.00mm:PinHeader_1x01_P1.00mm_Vertical
cr | cr10 | Connector_PinHeader_1.00mm:PinHeader_1x01_P1.00mm_Vertical
cr | cr11 | Connector_PinHeader_1.00mm:PinHeader_1x01_P1.00mm_Vertical
cr | cr12 | Connector_PinHeader_1.00mm:PinHeader_1x01_P1.00mm_Vertical
cr | cr13 | Connector_PinHeader_1.00mm:PinHeader_1x01_P1.00mm_Vertical
cr | cr14 | Connector_PinHeader_1.00mm:PinHeader_1x01_P1.00mm_Vertical
cr | cr15 | Connector_PinHeader_1.00mm:PinHeader_1x01_P1.00mm_Vertical
cr | cr16 | Connector_PinHeader_1.00mm:PinHeader_1x01_P1.00mm_Vertical
cr | cr17 | Connector_PinHeader_1.00mm:PinHeader_1x01_P1.00mm_Vertical
cr | cr18 | Connector_PinHeader_1.00mm:PinHeader_1x01_P1.00mm_Vertical
cr | cr19 | Connector_PinHeader_1.00mm:PinHeader_1x01_P1.00mm_Vertical
cr | cr20 | Connector_PinHeader_1.00mm:PinHeader_1x01_P1.00mm_Vertical
cr | cr21 | Connector_PinHeader_1.00mm:PinHeader_1x01_P1.00mm_Vertical
cr | cr22 | Connector_PinHeader_1.00mm:PinHeader_1x01_P1.00mm_Vertical
cr | cr23 | Connector_PinHeader_1.00mm:PinHeader_1x01_P1.00mm_Vertical
1N4148WS | D1 | Diode_SMD:D_SOD-323 | C2128
1N4148WS | D2 | Diode_SMD:D_SOD-323 | C2128
B5819W | D3 | Diode_SMD:D_SOD-123 | C8598
LED-GREEN-0603 | D4 | LED_SMD:LED_0603_1608Metric | C72043
LED-GREEN-0603 | D5 | LED_SMD:LED_0603_1608Metric | C72043
LED-GREEN-0603 | D6 | LED_SMD:LED_0603_1608Metric | C72043
LED-WHITE-0603 | D7 | LED_SMD:LED_0603_1608Metric | C84265
B5819W | D8 | Diode_SMD:D_SOD-123 | C8598
1N4148WS | D9 | hellen-one-common:SOD-323 | C2128
B5819W | D10 | Diode_SMD:D_SOD-123 | C8598
LED-RED-0603 | D11 | LED_SMD:LED_0603_1608Metric | C2286
LED-GREEN-0603 | D12 | LED_SMD:LED_0603_1608Metric | C72043
1N4148WS | D13 | Diode_SMD:D_SOD-323 | C2128
1N4148WS | D14 | Diode_SMD:D_SOD-323 | C2128
LED-RED-0603 | D15 | LED_SMD:LED_0603_1608Metric | C2286
LED-BLUE-0603 | D16 | LED_SMD:LED_0603_1608Metric | C72041
LED-BLUE-0603 | D17 | LED_SMD:LED_0603_1608Metric | C72041
LED-BLUE-0603 | D18 | LED_SMD:LED_0603_1608Metric | C72041
LED-BLUE-0603 | D19 | LED_SMD:LED_0603_1608Metric | C72041
LED-BLUE-0603 | D20 | LED_SMD:LED_0603_1608Metric | C72041
LED-BLUE-0603 | D21 | LED_SMD:LED_0603_1608Metric | C72041
LED-BLUE-0603 | D22 | LED_SMD:LED_0603_1608Metric | C72041
LED-BLUE-0603 | D23 | LED_SMD:LED_0603_1608Metric | C72041
LED-RED-0603 | D24 | LED_SMD:LED_0603_1608Metric | C2286
LED-RED-0603 | D25 | LED_SMD:LED_0603_1608Metric | C2286
LED-RED-0603 | D26 | LED_SMD:LED_0603_1608Metric | C2286
LED-RED-0603 | D27 | LED_SMD:LED_0603_1608Metric | C2286
LED-RED-0603 | D28 | LED_SMD:LED_0603_1608Metric | C2286
LED-RED-0603 | D29 | LED_SMD:LED_0603_1608Metric | C2286
LED-RED-0603 | D30 | LED_SMD:LED_0603_1608Metric | C2286
LED-RED-0603 | D31 | LED_SMD:LED_0603_1608Metric | C2286
1N4148WS | D32 | Diode_SMD:D_SOD-323 | C2128
1N4148WS | D33 | Diode_SMD:D_SOD-323 | C2128
1N4148WS | D34 | Diode_SMD:D_SOD-323 | C2128
1N4148WS | D35 | Diode_SMD:D_SOD-323 | C2128
1N4148WS | D36 | Diode_SMD:D_SOD-323 | C2128
1N4148WS | D37 | Diode_SMD:D_SOD-323 | C2128
1N4148WS | D38 | Diode_SMD:D_SOD-323 | C2128
1N4148WS | D39 | Diode_SMD:D_SOD-323 | C2128
1N4148WS | D40 | Diode_SMD:D_SOD-323 | C2128
1N4148WS | D42 | Diode_SMD:D_SOD-323 | C2128
1N4148WS | D43 | Diode_SMD:D_SOD-323 | C2128
B5819W | D44 | Diode_SMD:D_SOD-123 | C8598
10A | F1 | hellen-one-common:36911600000 | C354908
10A | F2 | hellen-one-common:36911600000 | C354908
10A | F3 | hellen-one-common:36911600000 | C354908
10A | F4 | hellen-one-common:36911600000 | C354908
10A | F5 | hellen-one-common:36911600000 | C354908
10A | F6 | hellen-one-common:36911600000 | C354908
10A | F7 | hellen-one-common:36911600000 | C354908
10A | F8 | hellen-one-common:36911600000 | C354908
LOGO | G1 | hellen-one-common:LOGO
LOGO | G2 | rusefi_lib:LOGO
PROTO_AREA | G3 | hellen-one-common:PROTO_AREA
PROTO_AREA | G4 | hellen-one-common:PROTO_AREA
PROTO_AREA | G6 | hellen-one-common:PROTO_AREA
PROTO_AREA | G7 | hellen-one-common:PROTO_AREA
MountingHole | H1 | MountingHole:MountingHole_4.3mm_M4_DIN965
MountingHole | H2 | MountingHole:MountingHole_4.3mm_M4_DIN965
USB_B_Mini | J1 | hellen-one-common:USB-MINI-B-VERTICAL | C13453
Conn_01x05 | J2 | Connector_PinHeader_2.00mm:PinHeader_1x05_P2.00mm_Vertical
Conn_01x05 | J4 | Connector_PinHeader_2.54mm:PinHeader_1x05_P2.54mm_Vertical
VRIN1 | J14 | Connector_PinHeader_1.00mm:PinHeader_1x01_P1.00mm_Vertical
VRIN2 | J15 | Connector_PinHeader_1.00mm:PinHeader_1x01_P1.00mm_Vertical
VROUT1 | J16 | Connector_PinHeader_1.00mm:PinHeader_1x01_P1.00mm_Vertical
XH-8A | J17 | kicad6:XH-8A | C10385
AudioJack_THR | J18 | hellen-one-common:Jack_3.5mm_PJ-3250-5A | C165947
MiniFit | J19 | Connector_Molex:Molex_Mini-Fit_Jr_5569-02A2_2x01_P4.20mm_Horizontal
ETB | J20 | Connector_PinHeader_2.54mm:PinHeader_1x06_P2.54mm_Vertical
PPS | J21 | Connector_PinHeader_2.54mm:PinHeader_1x04_P2.54mm_Vertical
Jumper_2_Open | JP1 | hellen-one-common:PAD-0805-PAD | C17477
Jumper_2_Open | JP2 | hellen-one-common:PAD-0805-PAD | C17477
Jumper_2_Open | JP3 | hellen-one-common:PAD-0805-PAD | C17477
Jumper_2_Open | JP4 | hellen-one-common:PAD-0805-PAD | C17477
Jumper_2_Open | JP5 | hellen-one-common:PAD-0805-PAD | C17477
Jumper_2_Open | JP6 | hellen-one-common:PAD-0805-PAD
Jumper_2_Open | JP7 | hellen-one-common:PAD-0805-PAD | C17477
Jumper_2_Open | JP8 | hellen-one-common:PAD-0805-PAD | C17477
Jumper_2_Open | JP14 | hellen-one-common:PAD-0805-PAD | C17477
Jumper_2_Open | JP16 | hellen-one-common:PAD-0805-PAD | C17477
Jumper_2_Open | JP17 | hellen-one-common:PAD-0805-PAD | C17477
Jumper_2_Open | JP20 | hellen-one-common:PAD-0805-PAD
Jumper_2_Open | JP21 | hellen-one-common:PAD-0805-PAD
Jumper_2_Open | JP26 | hellen-one-common:PAD-0805-PAD | C17477
Jumper_2_Open | JP27 | hellen-one-common:PAD-0805-PAD | C17477
Jumper_2_Open | JP29 | hellen-one-common:PAD-0805-PAD | C17477
Jumper_2_Open | JP31 | hellen-one-common:PAD-0805-PAD | C17477
Jumper_2_Open | JP32 | hellen-one-common:PAD-0805-PAD | C17477
Jumper_2_Open | JP33 | hellen-one-common:PAD-0805-PAD | C17477
Jumper_2_Open | JP35 | hellen-one-common:PAD-0805-PAD | C17477
Jumper_2_Open | JP36 | hellen-one-common:PAD-0805-PAD | C17477
Jumper_2_Open | JP41 | hellen-one-common:PAD-0805-PAD
Jumper_2_Open | JP42 | hellen-one-common:PAD-0805-PAD | C17477
Jumper_2_Open | JP43 | hellen-one-common:PAD-0805-PAD | C17477
Jumper_2_Open | JP46 | hellen-one-common:PAD-0805-PAD | C17477
Jumper_2_Open | JP47 | hellen-one-common:PAD-0805-PAD | C17477
Jumper_2_Open | JP48 | hellen-one-common:PAD-0805-PAD | C17477
Jumper_2_Open | JP54 | hellen-one-common:PAD-1206-PAD | C182446
Jumper_2_Open | JP56 | hellen-one-common:PAD-1206-PAD | C182446
Jumper_2_Open | JP59 | hellen-one-common:PAD-0805-PAD | C17477
Jumper_2_Open | JP73 | hellen-one-common:PAD-0805-PAD | C17477
Jumper_2_Open | JP77 | hellen-one-common:PAD-0805-PAD | C17477
Jumper_2_Open | JP78 | hellen-one-common:PAD-0805-PAD | C17477
Jumper_2_Open | JP85 | hellen-one-common:PAD-0805-PAD | C17477
Jumper_2_Open | JP86 | hellen-one-common:PAD-0805-PAD | C17477
IN_KNOCK1_RAW | KNOCK_RAW1 | Connector_PinHeader_1.00mm:PinHeader_1x01_P1.00mm_Vertical
IN_KNOCK2_RAW | KNOCK_RAW2 | Connector_PinHeader_1.00mm:PinHeader_1x01_P1.00mm_Vertical
Module-power12-0.2 | M1 | hellen-one-power12-0.2:power12
Module-can-0.1 | M2 | hellen-one-can-0.1:can
Module-wbo-0.3 | M3 | hellen-one-wbo-0.3:wbo
Module-can-0.1 | M4 | hellen-one-can-0.1:can
Module-power5-0.2 | M5 | hellen-one-power5-0.2:power5
Module-vr-0.1 | M6 | hellen-one-vr-0.1:vr
Module-input-0.1 | M7 | hellen-one-input-0.1:input
Module-knock-0.1 | M8 | hellen-one-knock-0.1:knock
Module-output-0.3 | M9 | hellen-one-output-0.3:output
Module-ign8-0.2 | M10 | hellen-one-ign8-0.2:ign8
Module-mcu144-0.6 | M11 | hellen-one-mcu-0.6:mcu
Module-knock-0.1 | M12 | hellen-one-knock-0.1:knock
Module-sd-0.1 | M13 | hellen-one-sd-0.1:sd
MMCU | MMCU1 | Connector_PinHeader_1.00mm:PinHeader_1x01_P1.00mm_Vertical
MMCU | MMCU2 | Connector_PinHeader_1.00mm:PinHeader_1x01_P1.00mm_Vertical
MMCU | MMCU3 | Connector_PinHeader_1.00mm:PinHeader_1x01_P1.00mm_Vertical
MMCU | MMCU4 | Connector_PinHeader_1.00mm:PinHeader_1x01_P1.00mm_Vertical
MMCU | MMCU5 | Connector_PinHeader_1.00mm:PinHeader_1x01_P1.00mm_Vertical
MMCU | MMCU6 | Connector_PinHeader_1.00mm:PinHeader_1x01_P1.00mm_Vertical
MMCU | MMCU7 | Connector_PinHeader_1.00mm:PinHeader_1x01_P1.00mm_Vertical
MMCU | MMCU8 | Connector_PinHeader_1.00mm:PinHeader_1x01_P1.00mm_Vertical
MMCU | MMCU9 | Connector_PinHeader_1.00mm:PinHeader_1x01_P1.00mm_Vertical
MMCU | MMCU10 | Connector_PinHeader_1.00mm:PinHeader_1x01_P1.00mm_Vertical
MMCU | MMCU11 | Connector_PinHeader_1.00mm:PinHeader_1x01_P1.00mm_Vertical
MMCU | MMCU12 | Connector_PinHeader_1.00mm:PinHeader_1x01_P1.00mm_Vertical
MMCU | MMCU13 | Connector_PinHeader_1.00mm:PinHeader_1x01_P1.00mm_Vertical
MMCU | MMCU14 | Connector_PinHeader_1.00mm:PinHeader_1x01_P1.00mm_Vertical
MMCU | MMCU15 | Connector_PinHeader_1.00mm:PinHeader_1x01_P1.00mm_Vertical
MMCU | MMCU16 | Connector_PinHeader_1.00mm:PinHeader_1x01_P1.00mm_Vertical
MMCU | MMCU18 | Connector_PinHeader_1.00mm:PinHeader_1x01_P1.00mm_Vertical
MMCU | MMCU22 | Connector_PinHeader_1.00mm:PinHeader_1x01_P1.00mm_Vertical
MMCU | MMCU23 | Connector_PinHeader_1.00mm:PinHeader_1x01_P1.00mm_Vertical
MMCU | MMCU24 | Connector_PinHeader_1.00mm:PinHeader_1x01_P1.00mm_Vertical
MMCU | MMCU25 | Connector_PinHeader_1.00mm:PinHeader_1x01_P1.00mm_Vertical
MMCU | MMCU26 | Connector_PinHeader_1.00mm:PinHeader_1x01_P1.00mm_Vertical
MMCU | MMCU27 | Connector_PinHeader_1.00mm:PinHeader_1x01_P1.00mm_Vertical
MMCU | MMCU28 | Connector_PinHeader_1.00mm:PinHeader_1x01_P1.00mm_Vertical
MMCU | MMCU29 | Connector_PinHeader_1.00mm:PinHeader_1x01_P1.00mm_Vertical
MMCU | MMCU30 | Connector_PinHeader_1.00mm:PinHeader_1x01_P1.00mm_Vertical
MMCU | MMCU31 | Connector_PinHeader_1.00mm:PinHeader_1x01_P1.00mm_Vertical
MMCU | MMCU32 | Connector_PinHeader_1.00mm:PinHeader_1x01_P1.00mm_Vertical
MMCU | MMCU35 | Connector_PinHeader_1.00mm:PinHeader_1x01_P1.00mm_Vertical
MMCU | MMCU38 | Connector_PinHeader_1.00mm:PinHeader_1x01_P1.00mm_Vertical
MMCU | MMCU40 | Connector_PinHeader_1.00mm:PinHeader_1x01_P1.00mm_Vertical
P | P1 | Connector_Pin:Pin_D1.0mm_L10.0mm
P | P2 | Connector_Pin:Pin_D1.0mm_L10.0mm
P | P3 | Connector_Pin:Pin_D1.0mm_L10.0mm
P | P4 | Connector_Pin:Pin_D1.0mm_L10.0mm
P | P5 | Connector_Pin:Pin_D1.0mm_L10.0mm
P | P6 | Connector_Pin:Pin_D1.0mm_L10.0mm
Motronic_88pin | PP1 | rusefi_lib_private:88pin_STS
NGD8201AN | Q1 | Package_TO_SOT_SMD:TO-252-2 | C151649
NGD8201AN | Q2 | Package_TO_SOT_SMD:TO-252-2 | C151649
NGD8201AN | Q3 | Package_TO_SOT_SMD:TO-252-2 | C151649
NGD8201AN | Q4 | Package_TO_SOT_SMD:TO-252-2 | C151649
NGD8201AN | Q5 | Package_TO_SOT_SMD:TO-252-2 | C151649
NGD8201AN | Q6 | Package_TO_SOT_SMD:TO-252-2 | C151649
NGD8201AN | Q7 | Package_TO_SOT_SMD:TO-252-2 | C151649
NGD8201AN | Q8 | Package_TO_SOT_SMD:TO-252-2 | C151649
AUIPS2041LTR | Q9 | Package_TO_SOT_SMD:SOT-223 | C113610
AUIPS2041LTR | Q10 | Package_TO_SOT_SMD:SOT-223 | C113610
10k | R1 | Resistor_SMD:R_0402_1005Metric | C60489
10k | R2 | Resistor_SMD:R_0402_1005Metric | C60489
750R | R3 | Resistor_SMD:R_0402_1005Metric | C25132
680k | R4 | hellen-one-common:R0603 | C25822
DNP | R5 | Resistor_SMD:R_0402_1005Metric
DNP | R6 | Resistor_SMD:R_0402_1005Metric
DNP | R7 | Resistor_SMD:R_2512_6332Metric | NA
DNP | R8 | Resistor_SMD:R_2512_6332Metric | NA
DNP | R9 | Resistor_SMD:R_2512_6332Metric | NA
DNP | R10 | Resistor_SMD:R_2512_6332Metric | NA
DNP | R11 | Resistor_SMD:R_2512_6332Metric | NA
DNP | R12 | Resistor_SMD:R_2512_6332Metric | NA
DNP | R13 | Resistor_SMD:R_2512_6332Metric | NA
DNP | R14 | Resistor_SMD:R_2512_6332Metric | NA
20k | R15 | Resistor_SMD:R_0402_1005Metric | C25765
680k | R16 | hellen-one-common:R0603 | C25822
22 | R17 | hellen-one-common:R0603 | C23345
22 | R18 | hellen-one-common:R0603 | C23345
22 | R19 | hellen-one-common:R0603 | C23345
22 | R20 | hellen-one-common:R0603 | C23345
22 | R21 | hellen-one-common:R0603 | C23345
22 | R22 | hellen-one-common:R0603 | C23345
22 | R23 | hellen-one-common:R0603 | C23345
22 | R24 | hellen-one-common:R0603 | C23345
680k | R25 | hellen-one-common:R0603 | C25822
DNP | R26 | hellen-one-common:R0603
2.7k | R27 | hellen-one-common:R0603 | C13167
100k | R28 | Resistor_SMD:R_0402_1005Metric | C106234
10k | R29 | Resistor_SMD:R_0402_1005Metric | C60489
100 | R30 | Resistor_SMD:R_0402_1005Metric | C106233
1k6 | R31 | Resistor_SMD:R_0402_1005Metric | C25931
5k1 | R32 | Resistor_SMD:R_0402_1005Metric | C25941
5k1 | R33 | Resistor_SMD:R_0402_1005Metric | C25941
2.7k | R34 | hellen-one-common:R0603 | C13167
DNP | R35 | hellen-one-common:R0603
4.7k | R42 | Resistor_SMD:R_0402_1005Metric | C25940
5k1 | R43 | Resistor_SMD:R_0402_1005Metric | C25941
1k | RN5 | Resistor_SMD:R_Array_Concave_4x0603 | C240722
1k | RN6 | Resistor_SMD:R_Array_Concave_4x0603 | C240722
4.7k | RN7 | Resistor_SMD:R_Array_Concave_4x0603 | C1980
4.7k | RN8 | Resistor_SMD:R_Array_Concave_4x0603 | C1980
Button_SPST | SW1 | hellen-one-common:SMD-2_2.9x3.9x1.7 | C115357
Button_SPST | SW2 | hellen-one-common:SMD-2_2.9x3.9x1.7 | C115357
TestPoint | TP1 | TestPoint:TestPoint_Pad_D1.0mm
TestPoint | TP2 | TestPoint:TestPoint_Pad_D1.0mm
TestPoint | TP3 | TestPoint:TestPoint_Pad_D1.0mm
TestPoint | TP4 | TestPoint:TestPoint_Pad_D1.0mm
MPXA6115A | U1 | Package_SO:SSO-8_6.8x5.9mm_P1.27mm_Clearance7mm
MPX4_MAP | U2 | rusefi_lib:MPX-4_MAP
LIS2DW12TR | U3 | hellen-one-common:LGA-12_2x2mm_P0.5mm | C189624
LPS25HB | U4 | Package_LGA:ST_HLGA-10_2.5x2.5mm_P0.6mm_LayoutBorder3x2y | C87898
MCP6002-xSN | U5 | Package_SO:SOIC-8_3.9x4.9mm_P1.27mm | C7377
L6205PD | U6 | hellen-one-common:SO20POWER | C36543
TLS115_SOIC | U7 | hellen-one-common:PG-DSO-8-43 | C540242
TLS115_SON | U8 | Package_SON:HVSON-8-1EP_3x3mm_P0.65mm_EP1.6x2.4mm
VIN8 | VIN1 | Connector_PinHeader_1.00mm:PinHeader_1x01_P1.00mm_Vertical
VIN8 | VIN2 | Connector_PinHeader_1.00mm:PinHeader_1x01_P1.00mm_Vertical
VIN8 | VIN3 | Connector_PinHeader_1.00mm:PinHeader_1x01_P1.00mm_Vertical
VIN8 | VIN4 | Connector_PinHeader_1.00mm:PinHeader_1x01_P1.00mm_Vertical
VIN8 | VIN5 | Connector_PinHeader_1.00mm:PinHeader_1x01_P1.00mm_Vertical
VIN8 | VIN6 | Connector_PinHeader_1.00mm:PinHeader_1x01_P1.00mm_Vertical
VIN8 | VIN8 | Connector_PinHeader_1.00mm:PinHeader_1x01_P1.00mm_Vertical
VIN9 | VIN9 | Connector_PinHeader_1.00mm:PinHeader_1x01_P1.00mm_Vertical
VIN10 | VIN10 | Connector_PinHeader_1.00mm:PinHeader_1x01_P1.00mm_Vertical
VIN16 | VIN16 | Connector_PinHeader_1.00mm:PinHeader_1x01_P1.00mm_Vertical
VIN17 | VIN17 | Connector_PinHeader_1.00mm:PinHeader_1x01_P1.00mm_Vertical
VOUT4 | VOUT2 | Connector_PinHeader_1.00mm:PinHeader_1x01_P1.00mm_Vertical
VOUT4 | VOUT3 | Connector_PinHeader_1.00mm:PinHeader_1x01_P1.00mm_Vertical
VOUT4 | VOUT4 | Connector_PinHeader_1.00mm:PinHeader_1x01_P1.00mm_Vertical
VOUT5 | VOUT5 | Connector_PinHeader_1.00mm:PinHeader_1x01_P1.00mm_Vertical
VOUT6 | VOUT6 | Connector_PinHeader_1.00mm:PinHeader_1x01_P1.00mm_Vertical
VOUT4 | VOUT7 | Connector_PinHeader_1.00mm:PinHeader_1x01_P1.00mm_Vertical
VOUT4 | VOUT8 | Connector_PinHeader_1.00mm:PinHeader_1x01_P1.00mm_Vertical
VOUT4 | VOUT9 | Connector_PinHeader_1.00mm:PinHeader_1x01_P1.00mm_Vertical
VOUT4 | VOUT10 | Connector_PinHeader_1.00mm:PinHeader_1x01_P1.00mm_Vertical
VOUT4 | VOUT11 | Connector_PinHeader_1.00mm:PinHeader_1x01_P1.00mm_Vertical
VOUT4 | VOUT12 | Connector_PinHeader_1.00mm:PinHeader_1x01_P1.00mm_Vertical
VOUT4 | VOUT13 | Connector_PinHeader_1.00mm:PinHeader_1x01_P1.00mm_Vertical
VOUT4 | VOUT14 | Connector_PinHeader_1.00mm:PinHeader_1x01_P1.00mm_Vertical
VOUT4 | VOUT15 | Connector_PinHeader_1.00mm:PinHeader_1x01_P1.00mm_Vertical
VOUT4 | VOUT16 | Connector_PinHeader_1.00mm:PinHeader_1x01_P1.00mm_Vertical
VOUT4 | VOUT17 | Connector_PinHeader_1.00mm:PinHeader_1x01_P1.00mm_Vertical
VOUT4 | VOUT18 | Connector_PinHeader_1.00mm:PinHeader_1x01_P1.00mm_Vertical
VOUT4 | VOUT19 | Connector_PinHeader_1.00mm:PinHeader_1x01_P1.00mm_Vertical
VOUT4 | VOUT20 | Connector_PinHeader_1.00mm:PinHeader_1x01_P1.00mm_Vertical
VOUT4 | VOUT21 | Connector_PinHeader_1.00mm:PinHeader_1x01_P1.00mm_Vertical
VOUT4 | VOUT22 | Connector_PinHeader_1.00mm:PinHeader_1x01_P1.00mm_Vertical
VOUT4 | VOUT23 | Connector_PinHeader_1.00mm:PinHeader_1x01_P1.00mm_Vertical
VOUT4 | VOUT24 | Connector_PinHeader_1.00mm:PinHeader_1x01_P1.00mm_Vertical
VOUT4 | VOUT25 | Connector_PinHeader_1.00mm:PinHeader_1x01_P1.00mm_Vertical
VOUT4 | VOUT26 | Connector_PinHeader_1.00mm:PinHeader_1x01_P1.00mm_Vertical
VOUT4 | VOUT27 | Connector_PinHeader_1.00mm:PinHeader_1x01_P1.00mm_Vertical

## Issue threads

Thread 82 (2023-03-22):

Something is funky with PNG

chuckwagoncomputing, 2023-03-22:
The components are not where they belong.
https://github.com/rusefi/hellen88bmw/blob/main/boards/hellen88bmw-c/board/hellen88bmw-c.png
I noticed this when testing hellen-one export scripts. I was comparing my output with the output in the repo. My output was correct, so either someone did the frame export wrong, or there's some bug that's been fixed since it was exported.

rusefillc, 2023-03-22:
@chuckwagoncomputing just pushed fresh framework stuff

rusefillc, 2023-03-22:
it has generated something fresh https://github.com/rusefi/hellen88bmw/commit/1b9764f3ea59727ad798e16315f23c75de213dfd

chuckwagoncomputing, 2023-03-22:
It didn't touch the PNG.

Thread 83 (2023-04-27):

high RPM was an issue, can we guess relevant capacitor?

rusefillc, 2023-04-27:
With all the recent experience adjusting capacitors and high RPM loss of trigger events, what cap shall we adjust on rev B?

Qwerty-OFF, 2023-04-28:
Capacitors CRANK (C202) and CAM (C200) 1nf, this is a good value

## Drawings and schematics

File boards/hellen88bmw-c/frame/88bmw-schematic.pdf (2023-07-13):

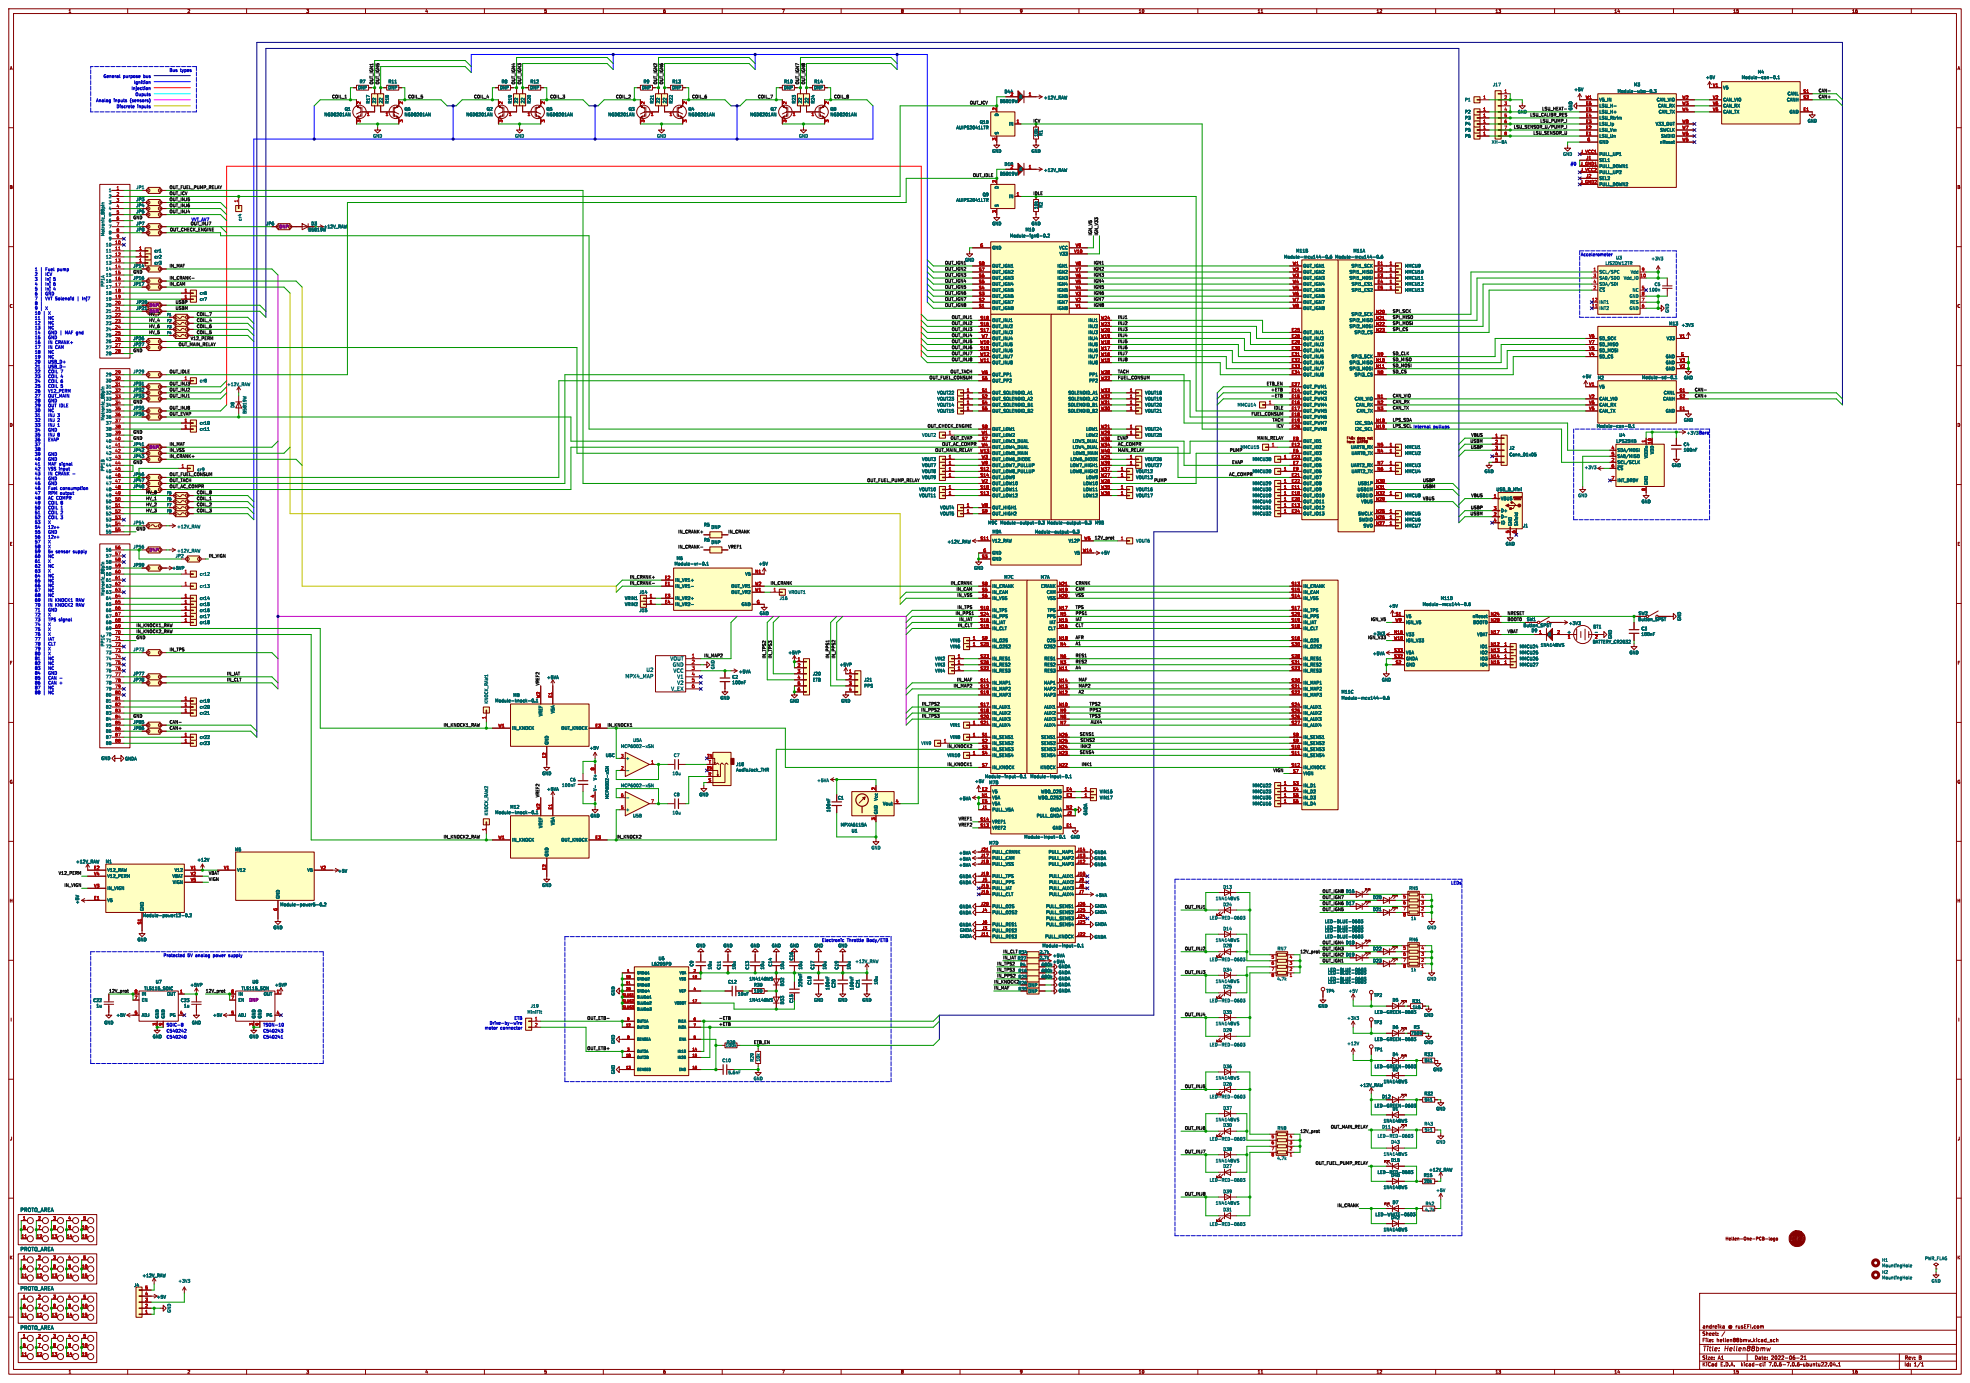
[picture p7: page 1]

40 | GND
41 | MAF signal 42 | VSS input 43 | IN CRANK - 44 | GND

45 | GND
46 | Fuel consumption
47 | RPM output 48 | AC COMPR

8 +5V M8 Module-knock-0.1 V5A E1 GND E2 OUT_KNOCK E3 IN_KNOCK W1 VREF W2 +5V M6 Module-vr-0.1

IAT N15 CLT N16 TPS N17 O2S N18 CAM

IAT CAM

1 KNOCK_RAW2 +5V V5A E1 GND E2 OUT_KNOCK E3 IN_KNOCK W1 VREF M8 W2 Module-knock-0.1

J26 PULL_RES2
GNDA GNDA

File: hellen88bmw.kicad_sch Sheet: / andreika @ rusEFI.com

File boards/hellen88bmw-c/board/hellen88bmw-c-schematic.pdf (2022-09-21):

# 9 PP¹A Motronic_88pin

# 1 VOUT3 10k R²

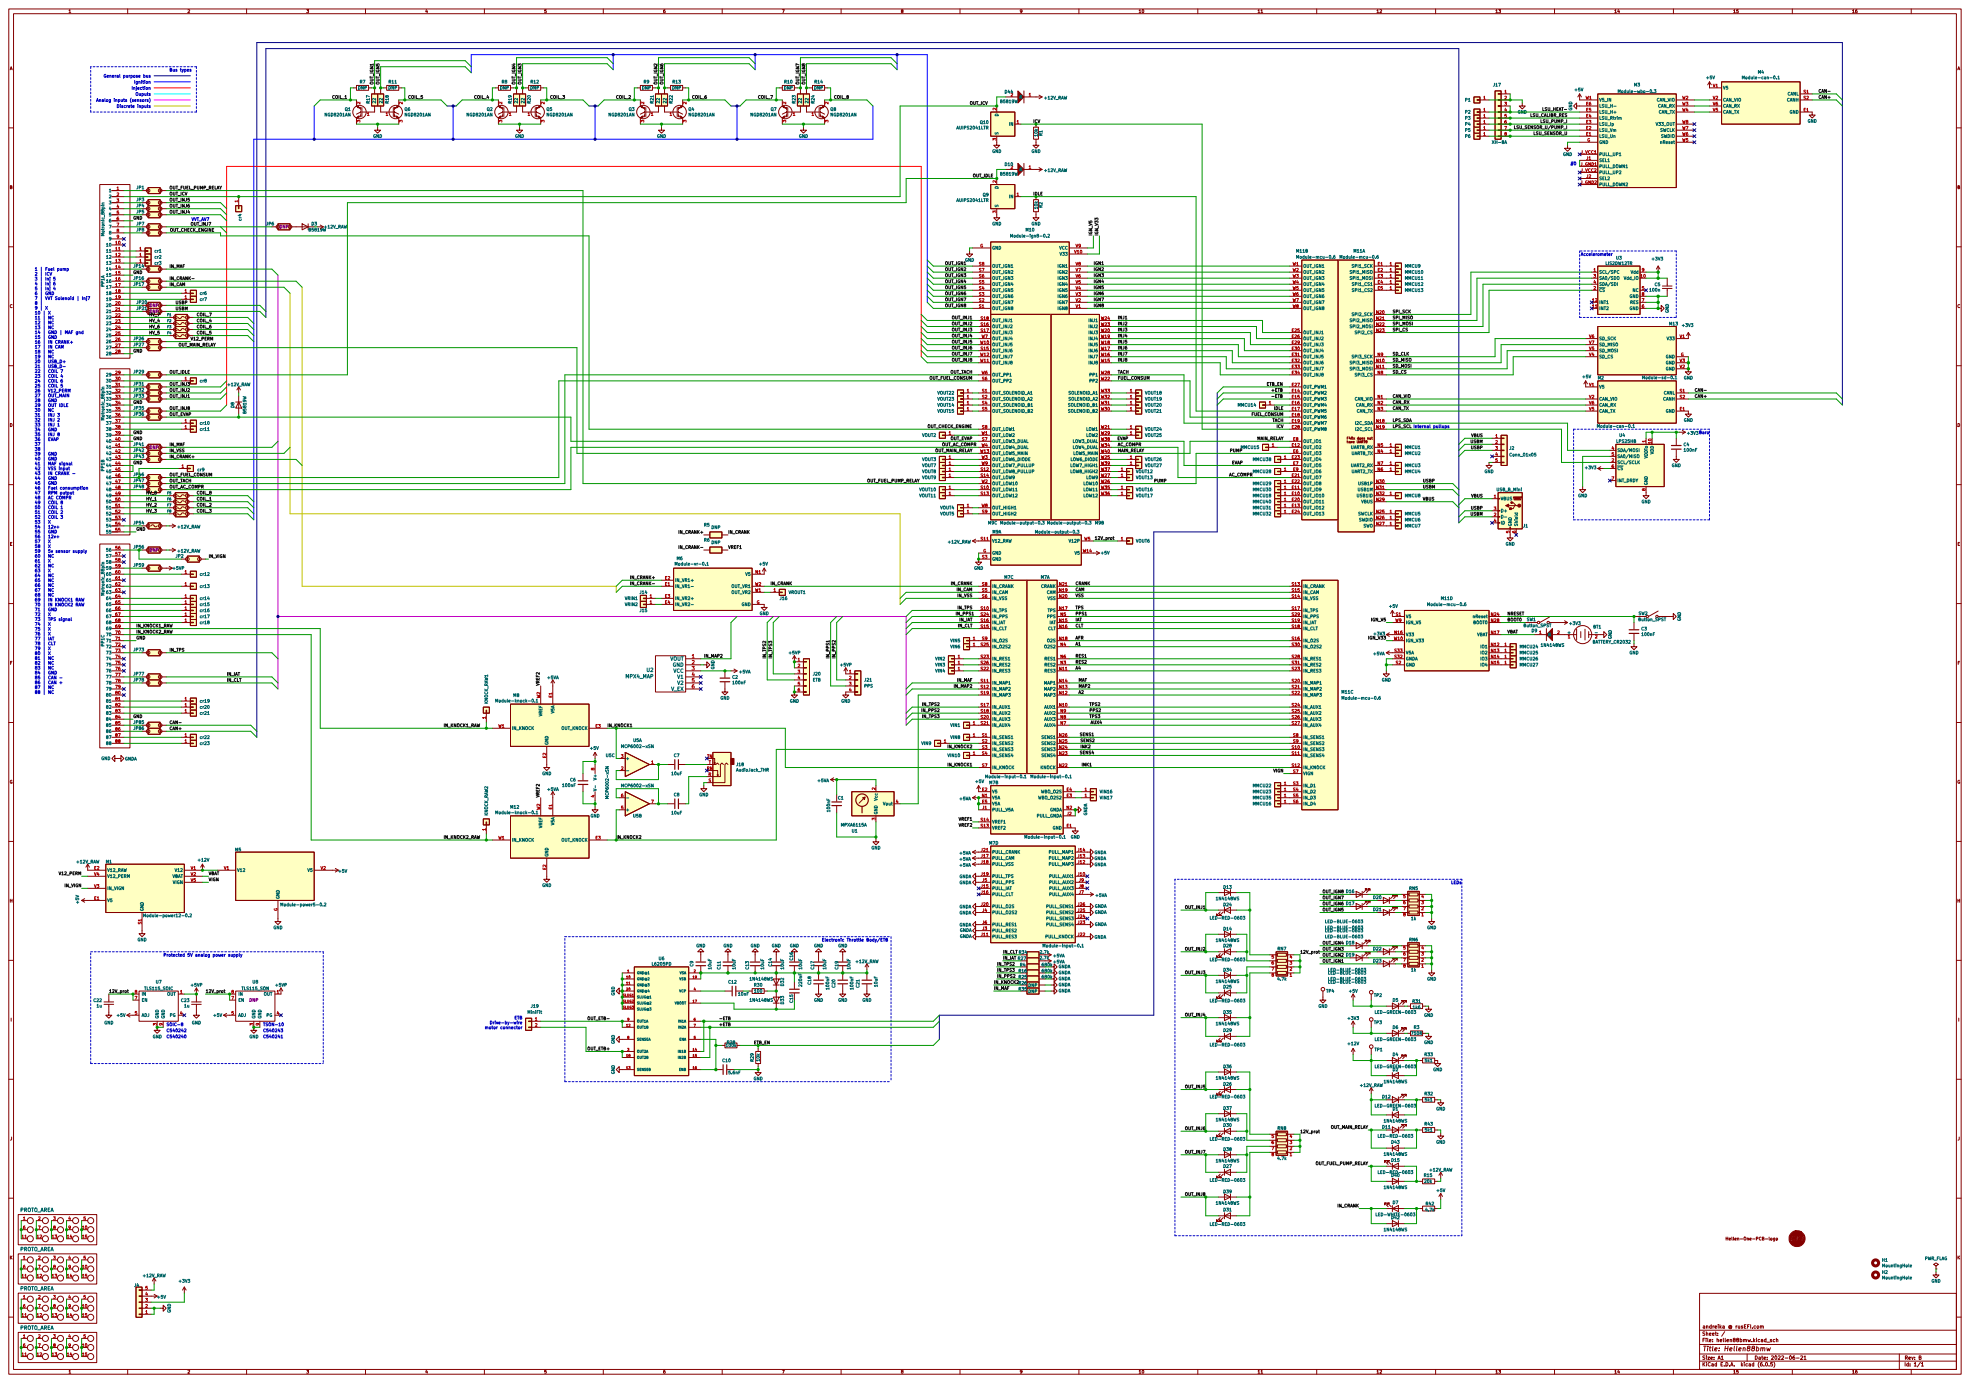
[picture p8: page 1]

N32 UART8_TX N4 UART8_RX N5 UART2_TX N6 UART2_RX N7 SPI3_CS N8 SPI3_SCK N9 M11A Module-mcu-0.6 OUT_IO10 E10 OUT_IO9 E11 OUT_IO2 E12 OUT_IO12 E13 OUT_PWM2 E14 OUT_PWM3 E15 OUT_PWM4 E16 OUT_PWM5 E17 OUT_PWM6 E18 OUT_PWM7 E19 OUT_IO11 E20 OUT_IO7 E21 OUT_IO8 E22 OUT_IO4 E23 OUT_IO13 E24 OUT_INJ1 E25 OUT_INJ2 E26 OUT_PWM1 E27 OUT_PWM8 E28 OUT_INJ3 E29 OUT_INJ4 E30 OUT_INJ5 E31 OUT_INJ6 E32 OUT_INJ7 E33 OUT_INJ8 E34 OUT_IO3 E6 OUT_IO5 E7 OUT_IO1 E8 OUT_IO6 E9 OUT_IGN1 W1 OUT_IGN2 W2 OUT_IGN3 W3 OUT_IGN4 W4 OUT_IGN5 W5 OUT_IGN6 W6 OUT_IGN7 W7 OUT_IGN8 W8M11B Module-mcu-0.6 GND

12V_prot
N19 VSS N20 CRANK N21 KNOCK N22 SENS4 N23 SENS3 N24 SENS2 N25 SENS1 N26 RES2 N3 O2S2 N4 PPS N5 RES1 N6 AUX4 N7 AUX3 N8 AUX2 N9 M7A Module-input-0.1 PULL_AUX1
IAT N15 CLT N16 TPS N17 O2S N18 CAM

1 KNOCK_RAW1+5VAV5A E1 GND E2 OUT_KNOCK E3 IN_KNOCK W1 VREF M8 W2 Module-knock-0.1

ETB Drive-by-wire motor connector

File: hellen88bmw.kicad_sch Sheet: / andreika @ rusEFI.com

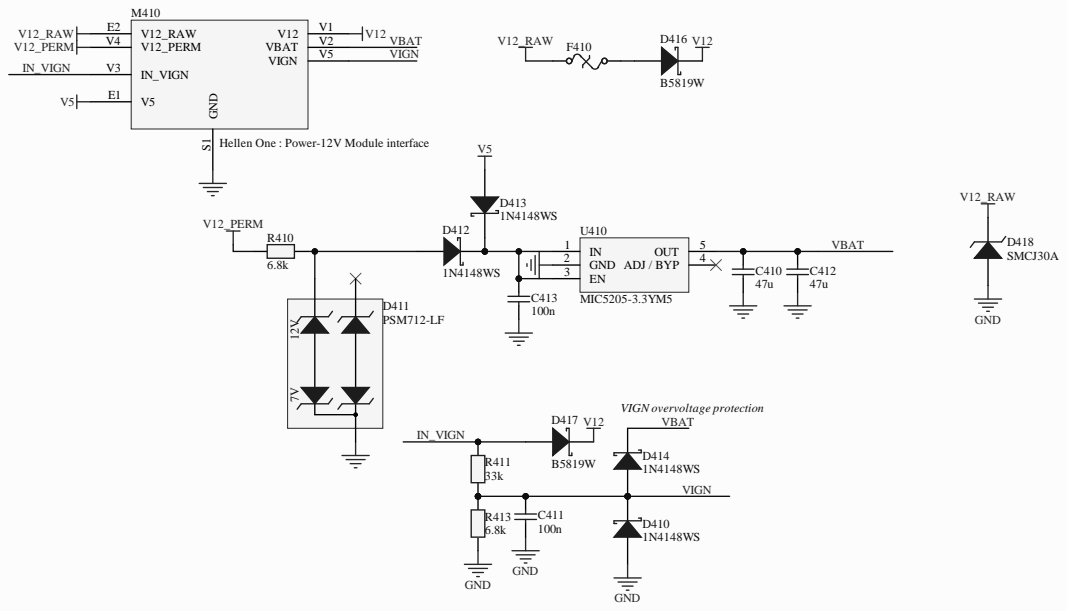
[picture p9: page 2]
tfo rm m/s/h; Hellen-One Power1 2; dreik; Size:; Date:; Rev; Shee; VBA; GND S1; Hel; len O; wer-1; terface; VIGN; overvo; tect; 8 SMCJ; 1 PSM7; MIC5

rusEFI EMS https://rusefi.co
Hellen-One

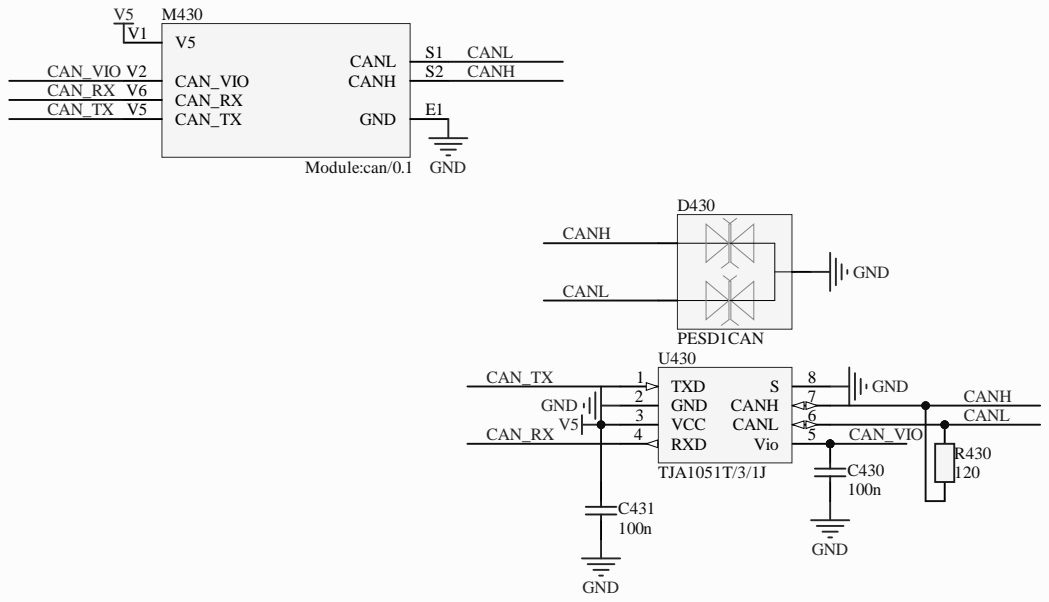
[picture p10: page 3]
andreika; Size:; Author:; Revision:; Sheet; PESD1CAN; GND; CANH; CANL; TXD 1 GND 2 VCC 3; Vio; 5 RXD 4; 6 CANH; TJA1051T/3/1J; CANH CANL; CAN_TX; CAN_RX; CAN_VIO; CAN_VIO V2; S2 CANL; CAN_TX V5; CAN_RX V6; Module:can/0.1

Hellen-One CAN
Title:

rusEFI EMS
Hellen-One Platform
https://rusefi.com/s/hellen72

1kR600

3.3k R623

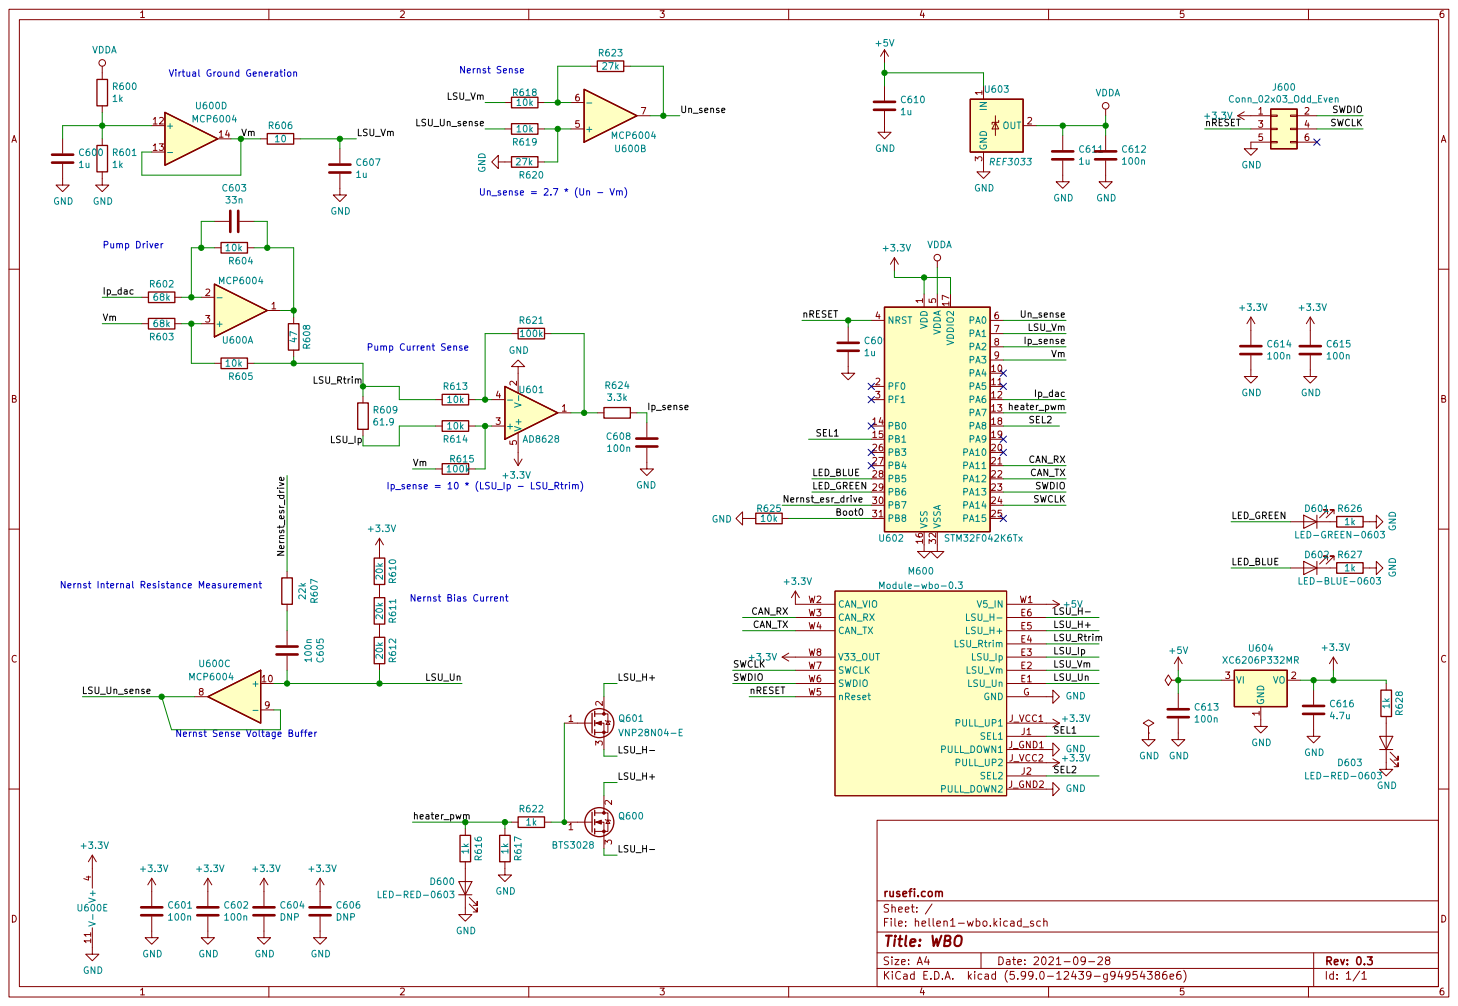
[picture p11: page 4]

Pump Current Sense Nernst Sense

LSU_Vm
Pump Driver Nernst Internal Resistance Measurement

1 VO 2 VI 3 U604 XC6206P332MR GND GND

1 PA4 10 PA5 11 PA6 12 PA7 13 PB0 14 PB1 15 VSS 16 VDDIO2 17 PA8 18 PA9 19 PF0 2 PA10 20 PA11 21 PA12 22 PA13 23 PA14 24 PA15 25 PB3 26 PB4 27 PB5 28 PB6 29 PF1 3 PB7 30 PB8 31 VSSA 32 NRST 4 VDDA

LED-RED-0603 ¹⁰⁰n C⁶⁰⁵ C604 DNP

Nernst Sense Voltage Buffer

1k GND GND R⁶¹⁶ ¹k

File: hellen1-wbo.kicad_sch Sheet: / rusefi.com

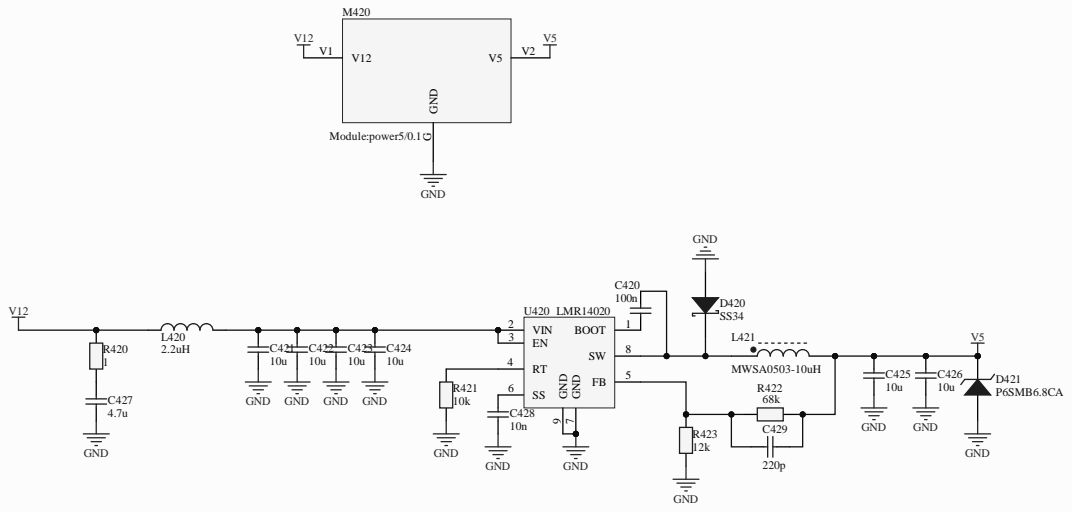
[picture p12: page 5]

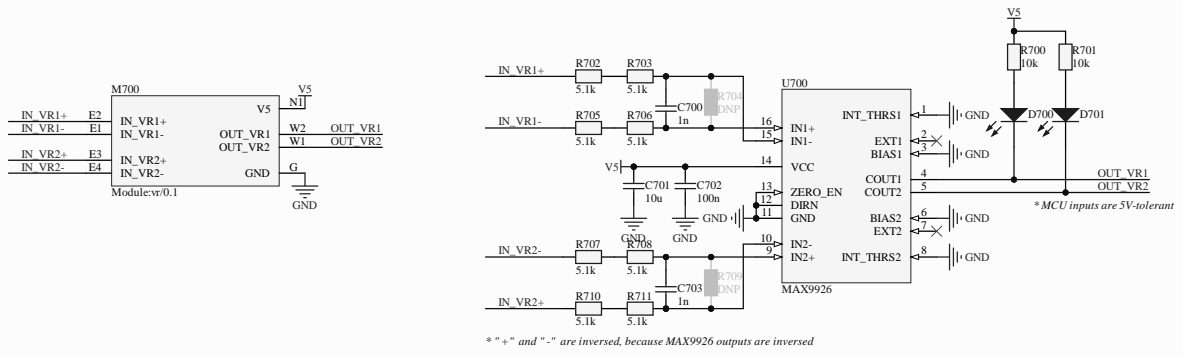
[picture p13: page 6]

* MCU inputs are 5V-tolerant

* " +" and " -" are inversed, because MAX9926 outputs are inversed

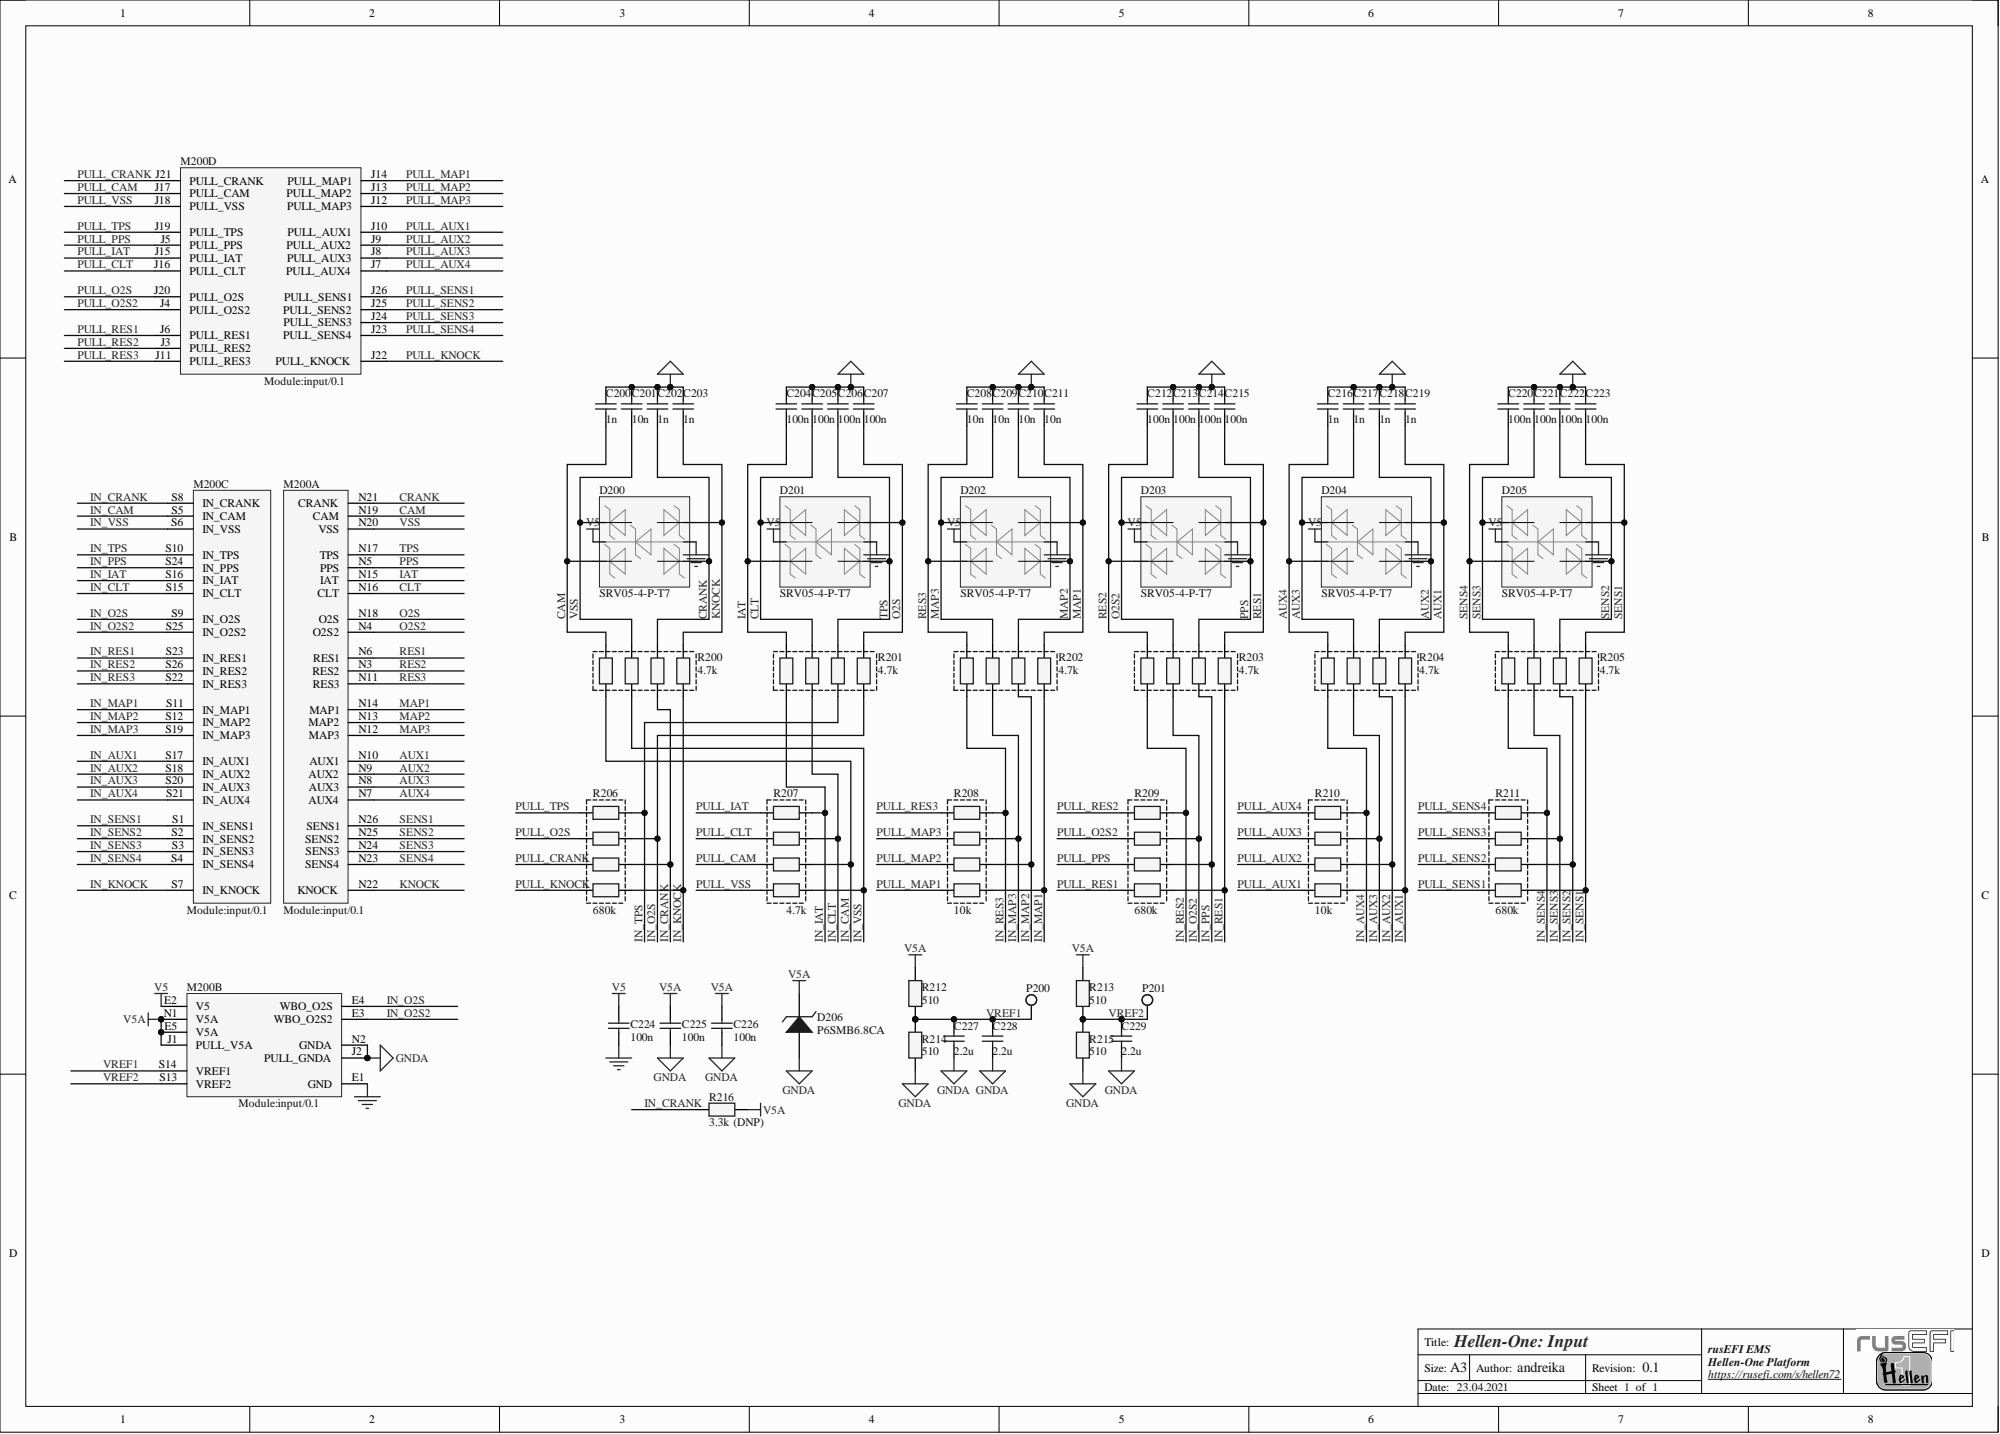
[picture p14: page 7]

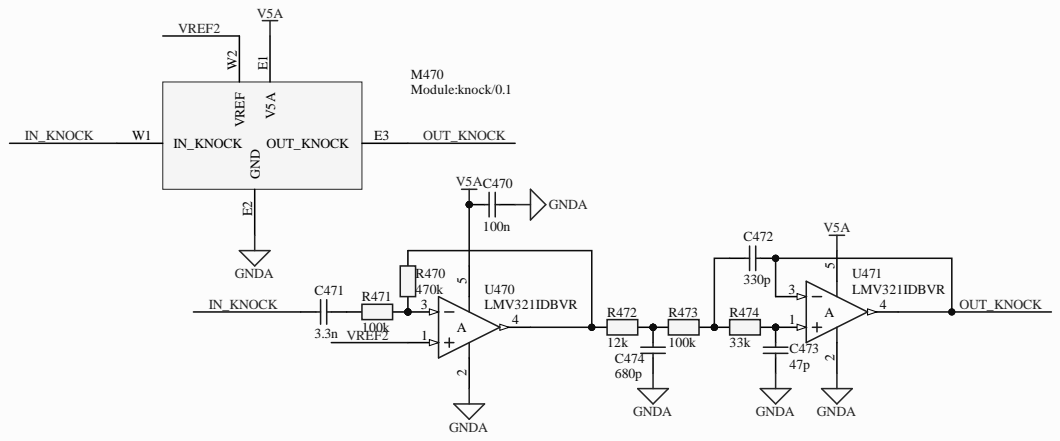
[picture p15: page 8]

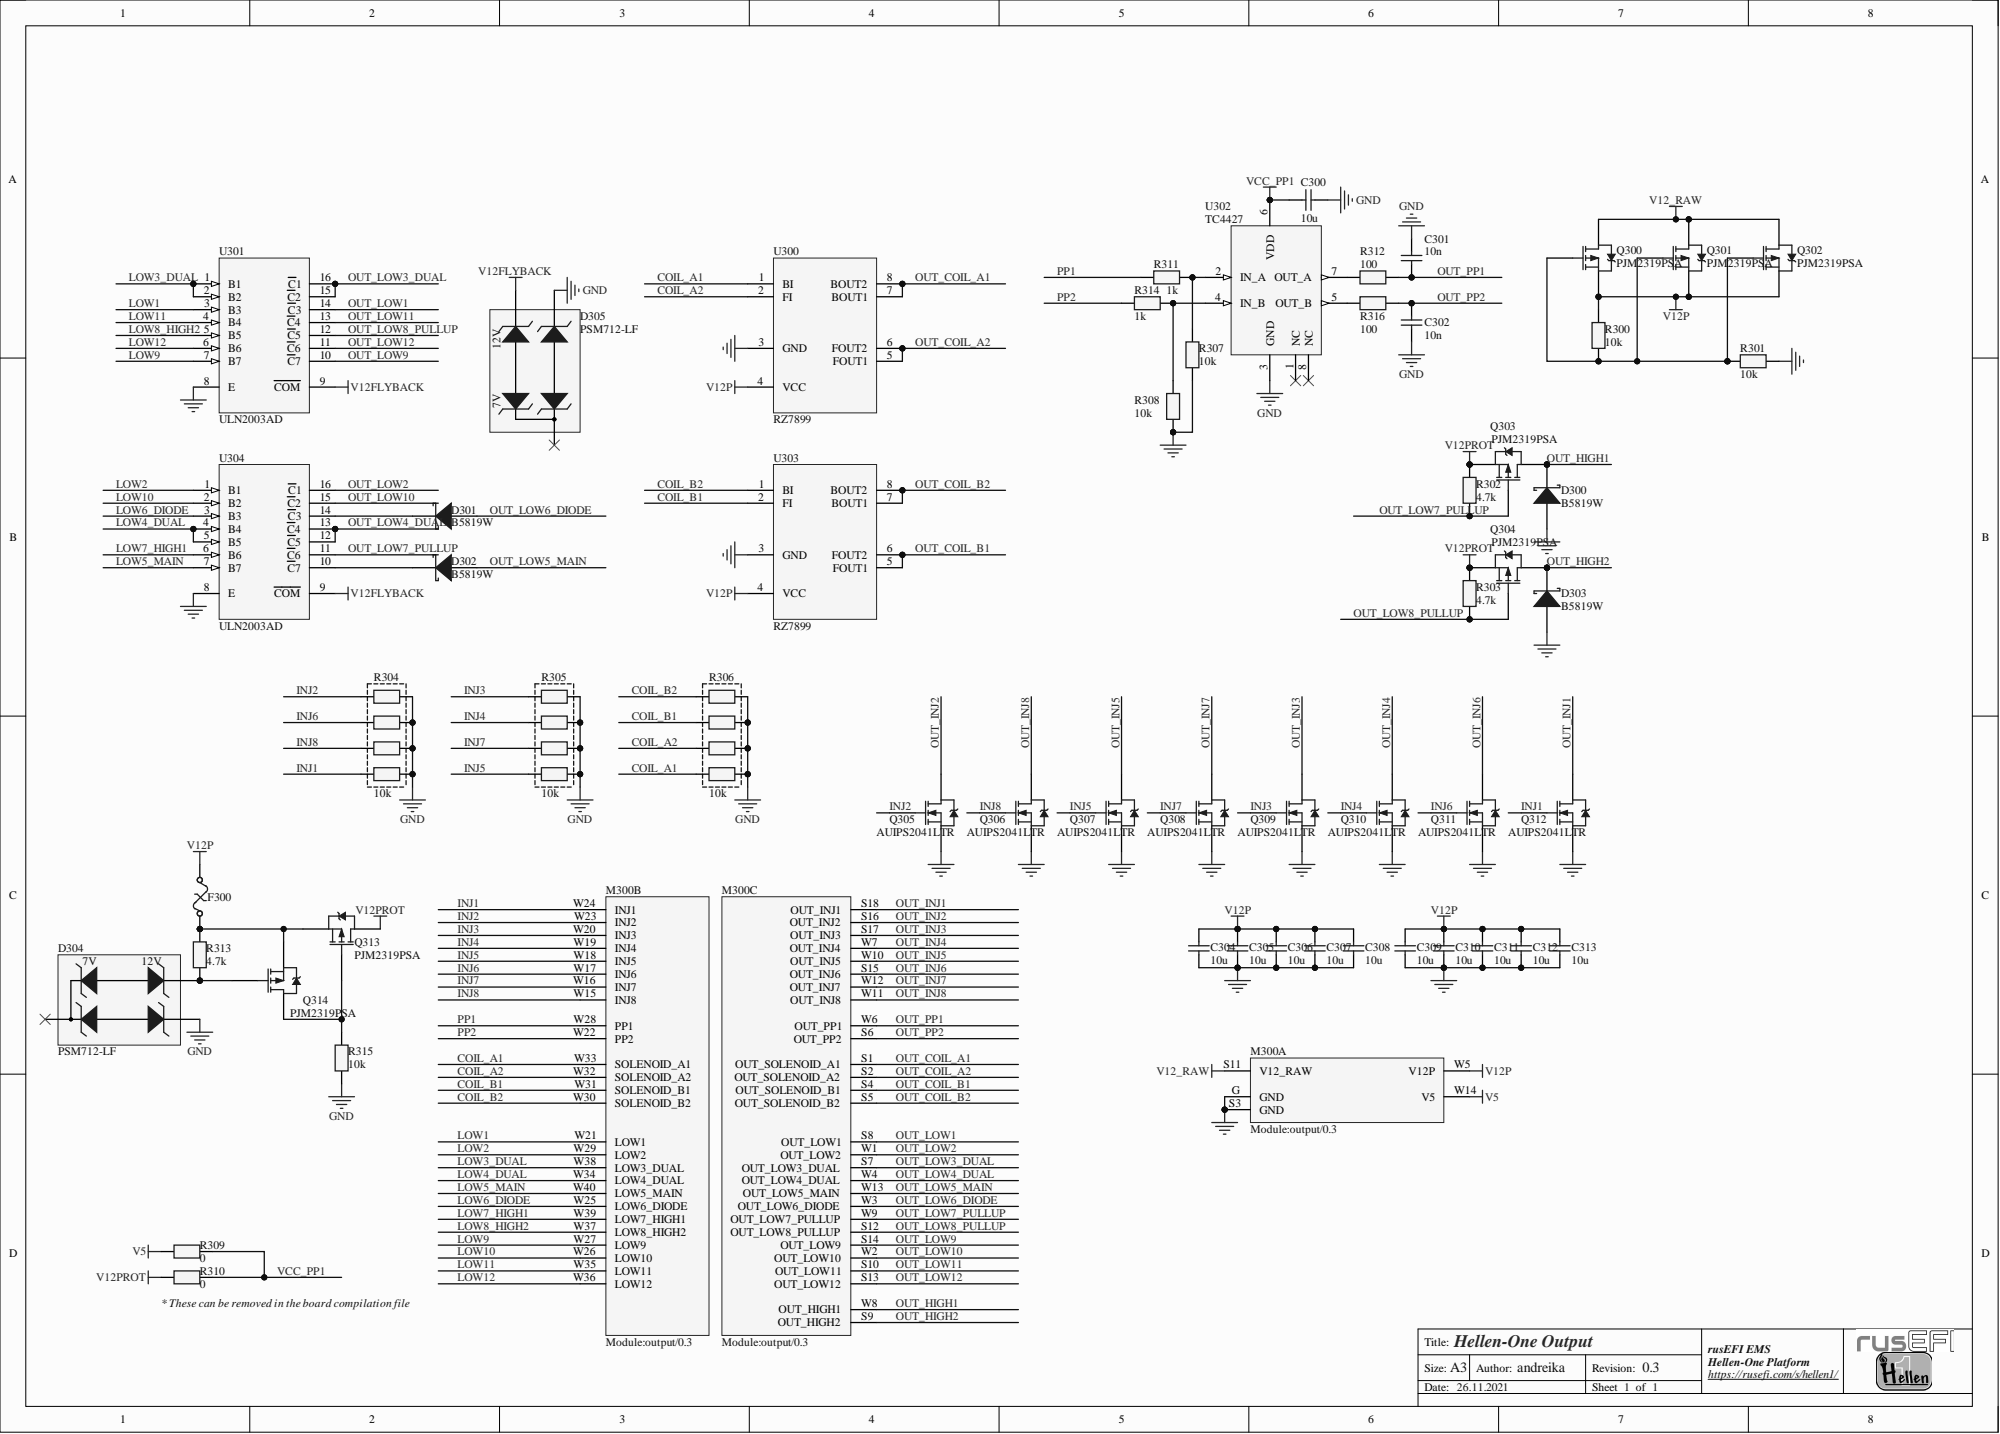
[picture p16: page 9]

* These can be removed in the board compilation file

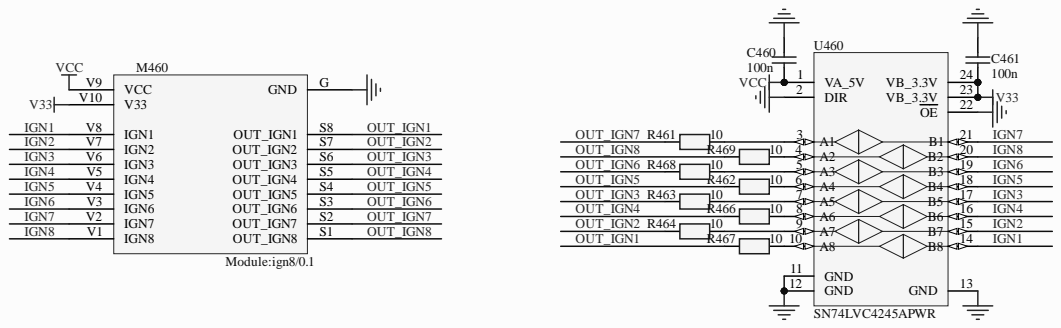
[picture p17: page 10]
tfo rm m/s/h; Size; Dat; Rev; Shee; _IGN; VCC; DIR; LVC4

Hellen-One IGN8 andreika

rusEFI EMS https://rusefi.co
Hellen-One

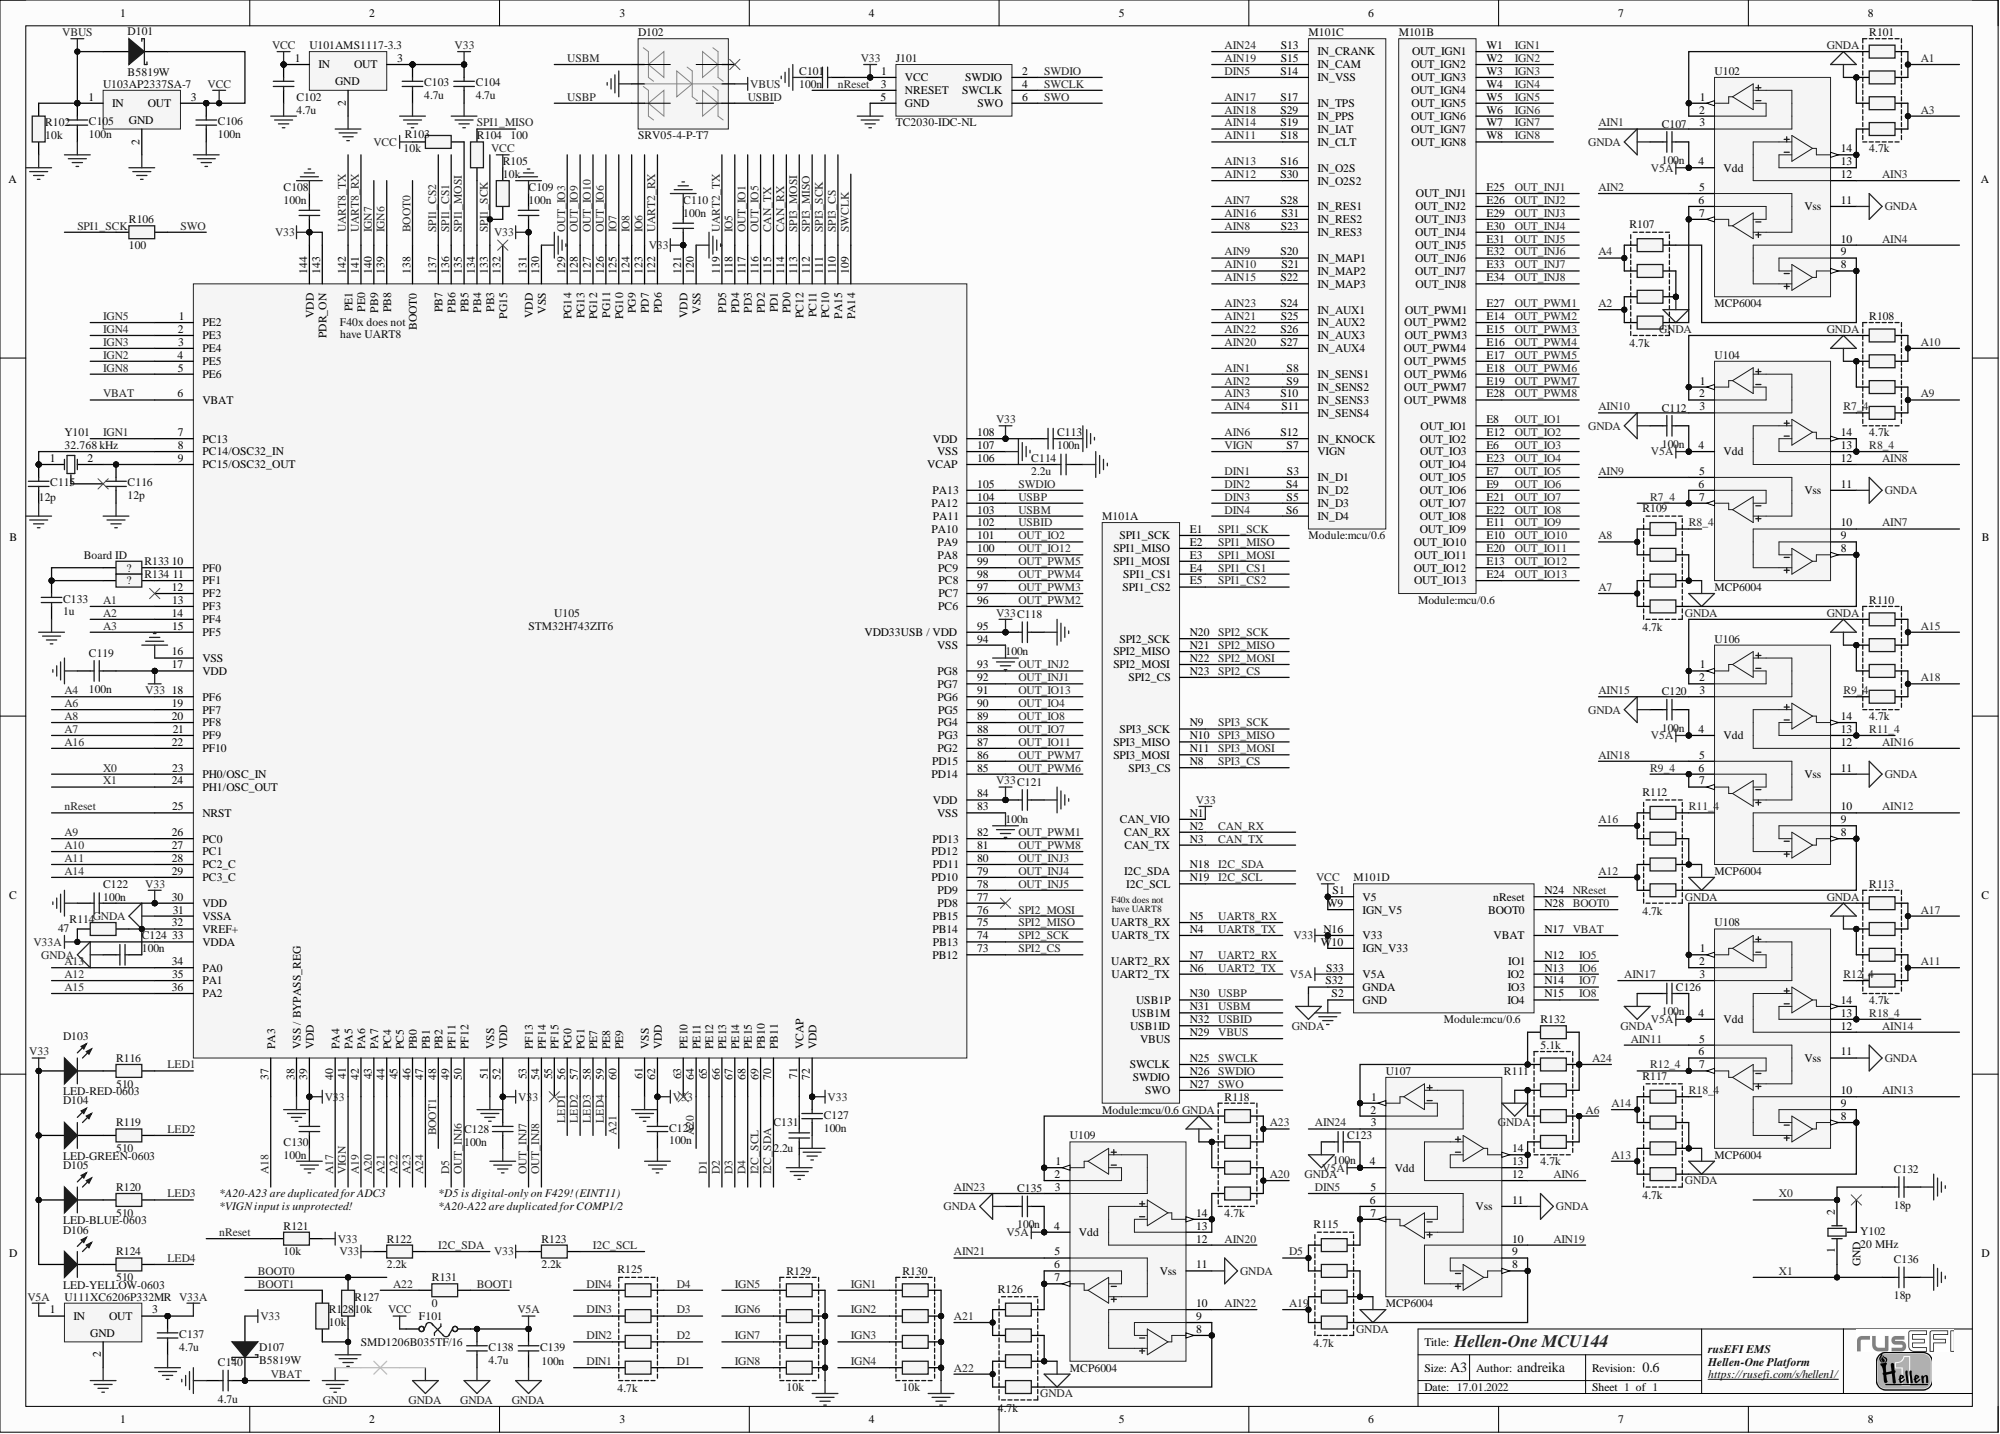
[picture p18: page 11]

D5 *D5 is digital-only on F429!(EINT11)

*A20-A23 are duplicated for ADC3
*VIGN input is unprotected!

2 SPI_I; 3 GND; 4 VCC; 5 SPI_SCK; 6 GND; 7 SPI_O; Molex MicroSD 47219-2001; GND; SD_CS SD_MOSI; SD_SCK; SD_MISO; V2 GND; SD_MOSI V5; SD_SCK V6 SD_MISO V7; Module:sd/0.1; SD_MOSI; SD_SCK SD_MISO

Hellen-One SD-Card

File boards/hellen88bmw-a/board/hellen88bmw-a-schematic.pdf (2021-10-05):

# 8 Vdd

# 100n GND G


GND ²²R²⁰ R12 DNP R8 DNP R¹⁹ 22

S11 GND
V12_RAW
N19 VSS N20 CRANK N21 KNOCK N22 SENS4 N23 SENS3 N24 SENS2 N25 SENS1 N26 RES2 N3 O2S2 N4 PPS N5 RES1 N6 AUX4 N7 AUX3 N8 AUX2 N9 M7A Module-input-0.1
IAT N15 CLT N16 TPS N17 O2S N18 CAM

Hellen-One-PCB-logo

File: hellen88bmw.kicad_sch Sheet: / andreika @ rusEFI.com

tfo rm m/s/h; Hellen-One Power1 2; dreik; Size:; Date:; Rev; Shee; VBA; GND S1; Hel; len O; wer-1; terface; VIGN; overvo; tect; 8 SMCJ; 1 PSM7; MIC5

rusEFI EMS https://rusefi.co
Hellen-One

andreika; Size:; Author:; Revision:; Sheet; PESD1CAN; GND; CANH; CANL; TXD 1 GND 2 VCC 3; Vio; 5 RXD 4; 6 CANH; TJA1051T/3/1J; CANH CANL; CAN_TX; CAN_RX; CAN_VIO; CAN_VIO V2; S2 CANL; CAN_TX V5; CAN_RX V6; Module:can/0.1

Hellen-One CAN
Title:

rusEFI EMS
Hellen-One Platform
https://rusefi.com/s/hellen72

1kR600

3.3k R623


Pump Current Sense Nernst Sense

LSU_Vm
Pump Driver Nernst Internal Resistance Measurement

1 VO 2 VI 3 U604 XC6206P332MR GND GND

1 PA4 10 PA5 11 PA6 12 PA7 13 PB0 14 PB1 15 VSS 16 VDDIO2 17 PA8 18 PA9 19 PF0 2 PA10 20 PA11 21 PA12 22 PA13 23 PA14 24 PA15 25 PB3 26 PB4 27 PB5 28 PB6 29 PF1 3 PB7 30 PB8 31 VSSA 32 NRST 4 VDDA

LED-RED-0603 ¹⁰⁰n C⁶⁰⁵ C604 DNP

Nernst Sense Voltage Buffer

1k GND GND R⁶¹⁶ ¹k

File: hellen1-wbo.kicad_sch Sheet: / rusefi.com



* MCU inputs are 5V-tolerant

* " +" and " -" are inversed, because MAX9926 outputs are inversed




* These can be removed in the board compilation file

tfo rm m/s/h; Size:; Rev; Shee; VCC; APW

Hellen-One IGN8 andreika

rusEFI EMS https://rusefi.co
Hellen-One


D5 *D5 is digital-only on F429!(EINT11)

*A20-A23 are duplicated for ADC3
*VIGN input is unprotected!

2 SPI_I; 3 GND; 4 VCC; 5 SPI_SCK; 6 GND; 7 SPI_O; Molex MicroSD 47219-2001; GND; SD_CS SD_MOSI; SD_SCK; SD_MISO; V2 GND; SD_MOSI V5; SD_SCK V6 SD_MISO V7; Module:sd/0.1; SD_MOSI; SD_SCK SD_MISO

Hellen-One SD-Card

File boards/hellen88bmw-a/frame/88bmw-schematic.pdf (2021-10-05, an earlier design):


Hellen-One-PCB-logo

File: hellen88bmw.kicad_sch Sheet: / andreika @ rusEFI.com

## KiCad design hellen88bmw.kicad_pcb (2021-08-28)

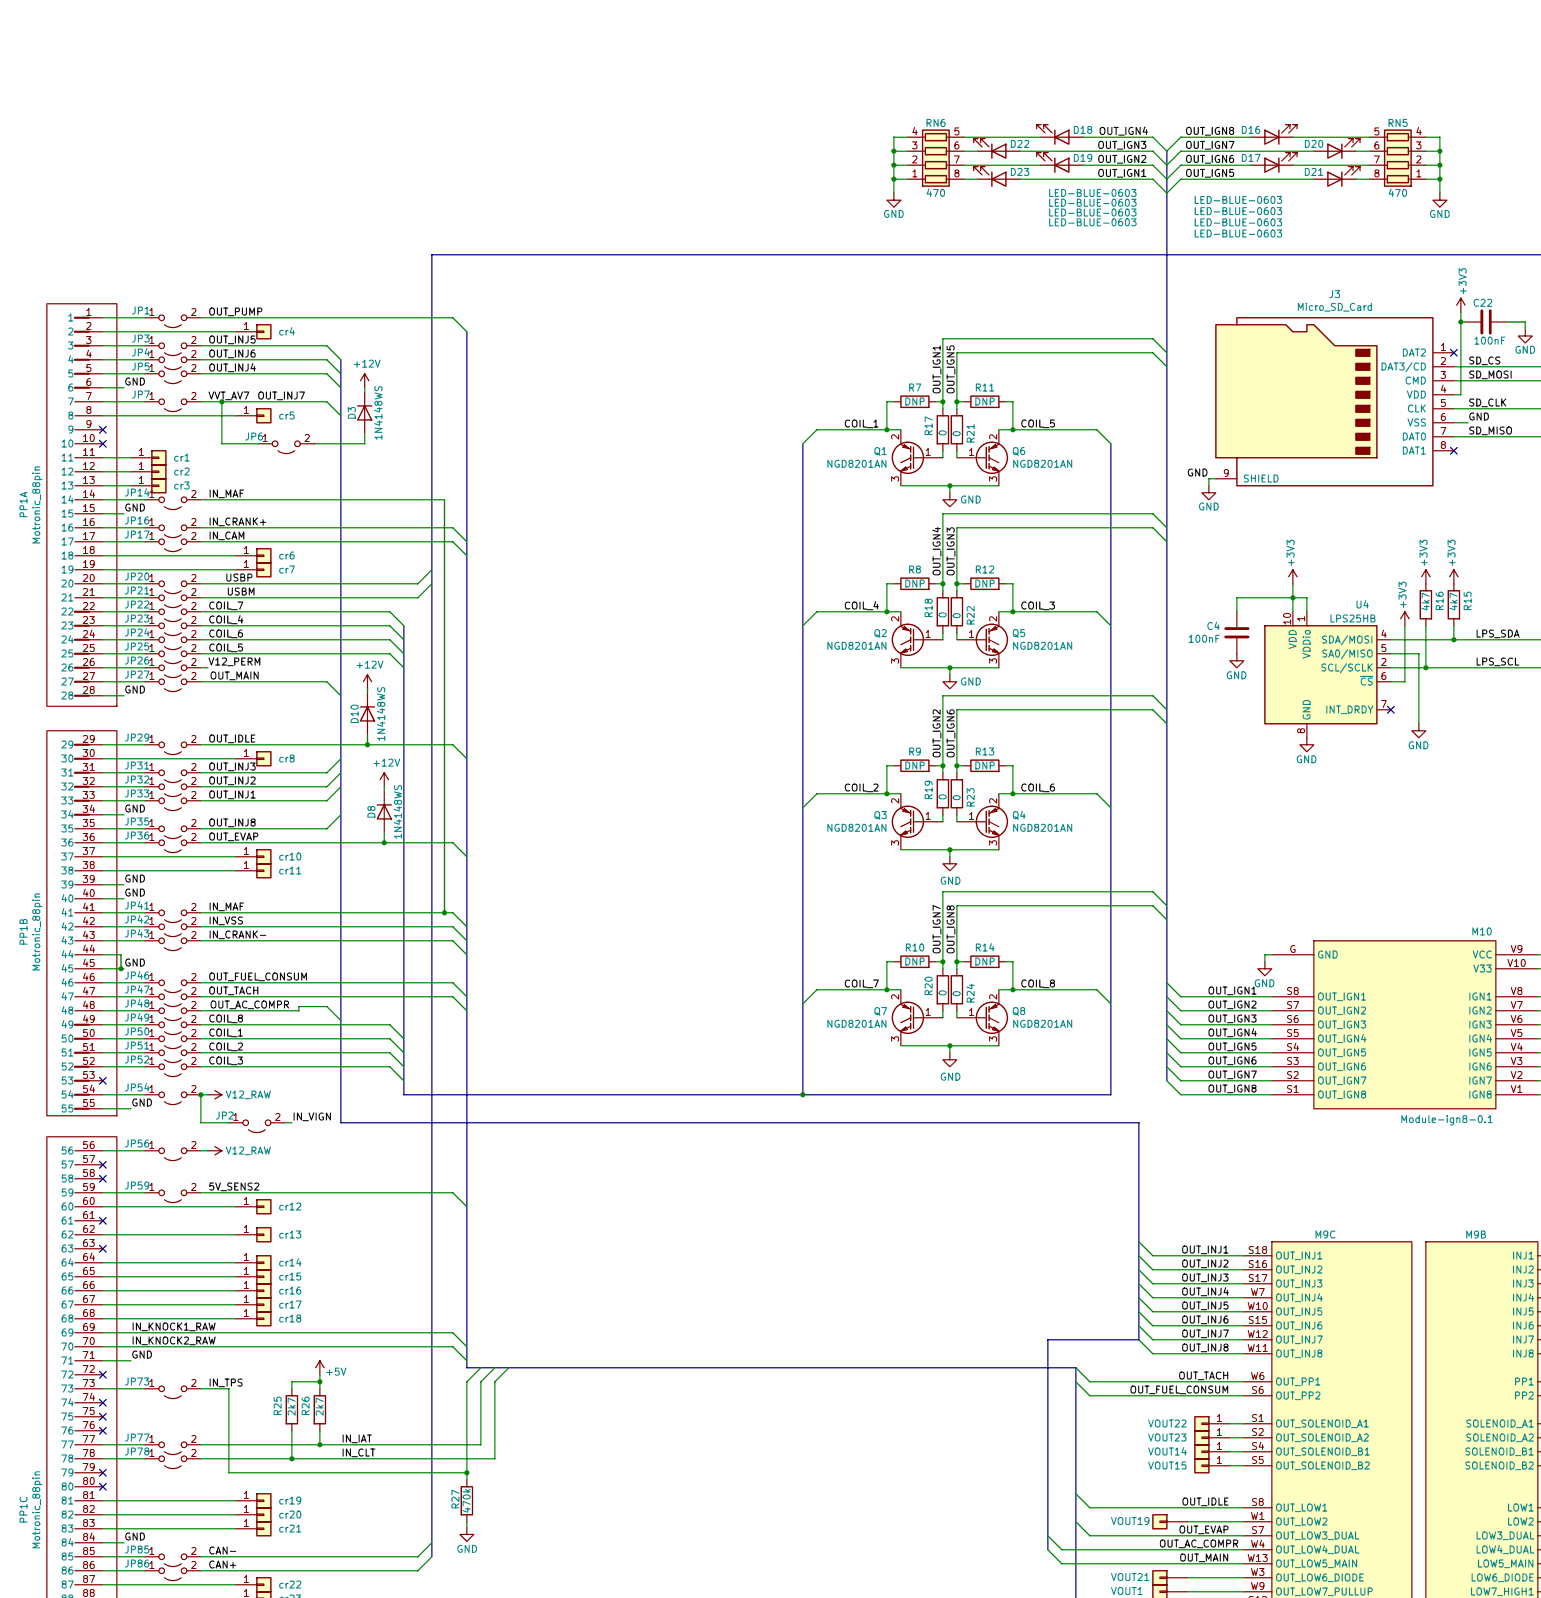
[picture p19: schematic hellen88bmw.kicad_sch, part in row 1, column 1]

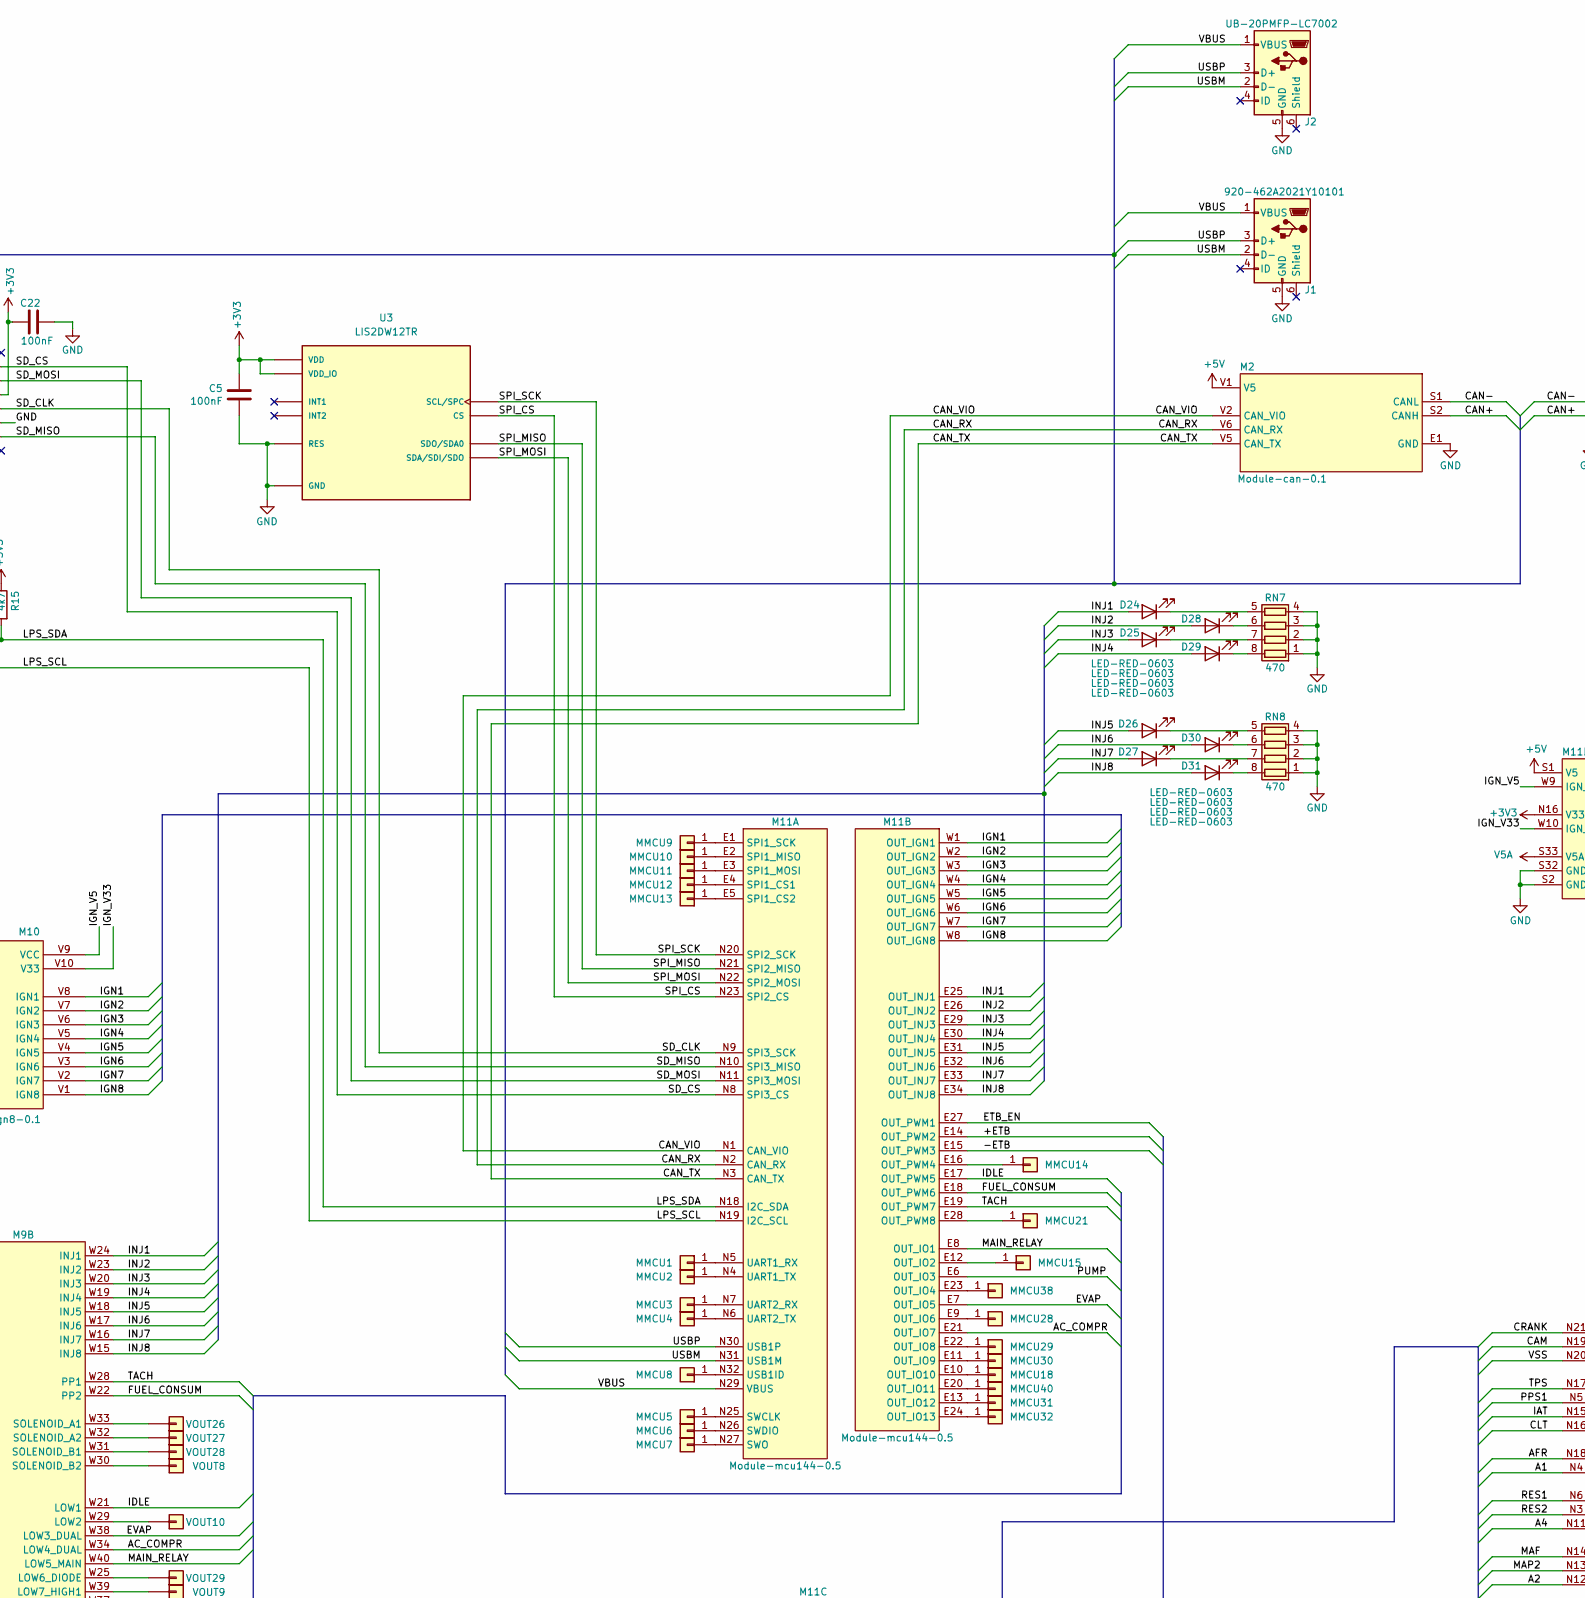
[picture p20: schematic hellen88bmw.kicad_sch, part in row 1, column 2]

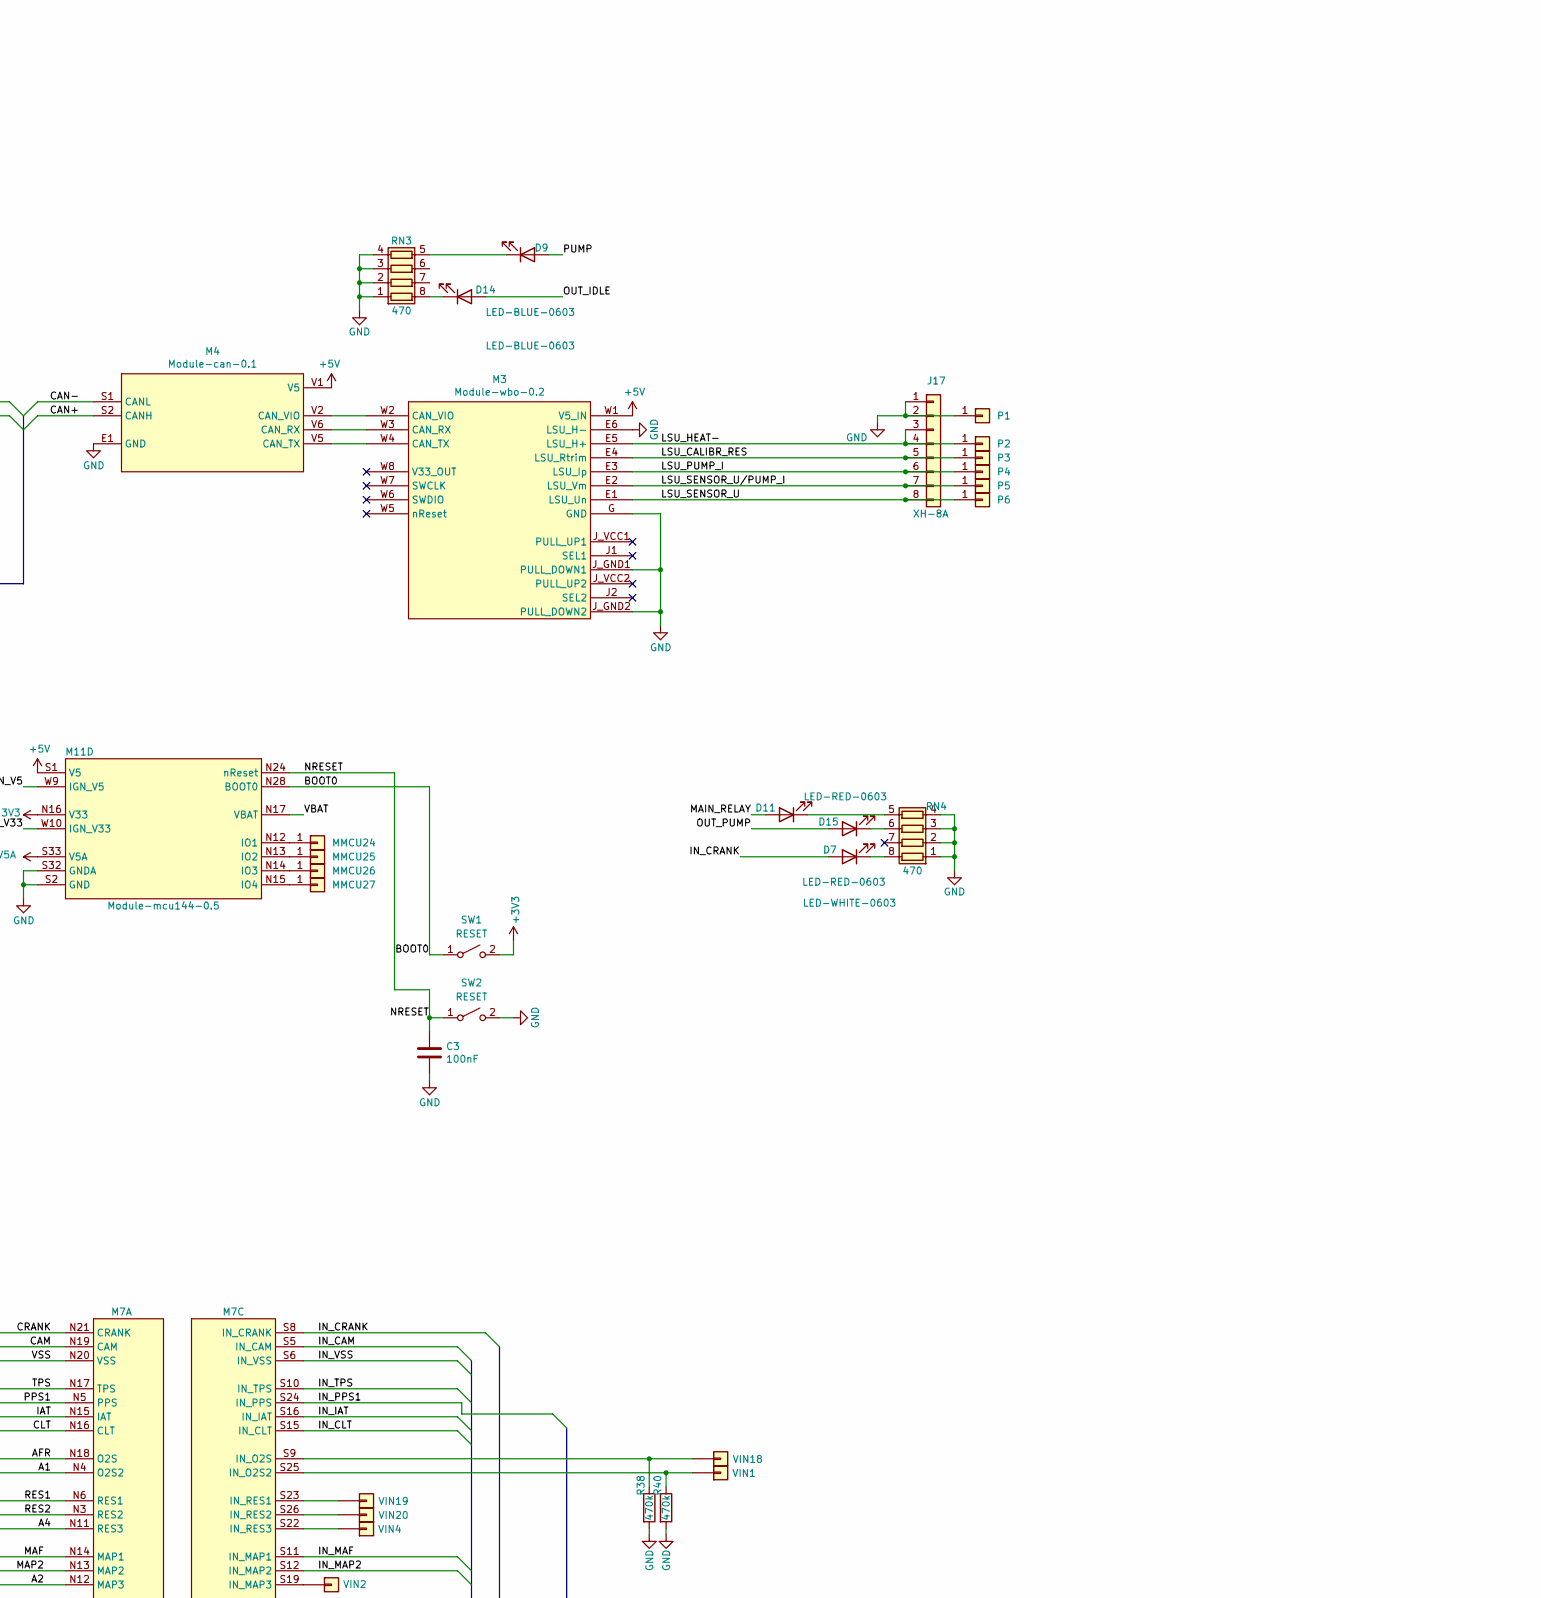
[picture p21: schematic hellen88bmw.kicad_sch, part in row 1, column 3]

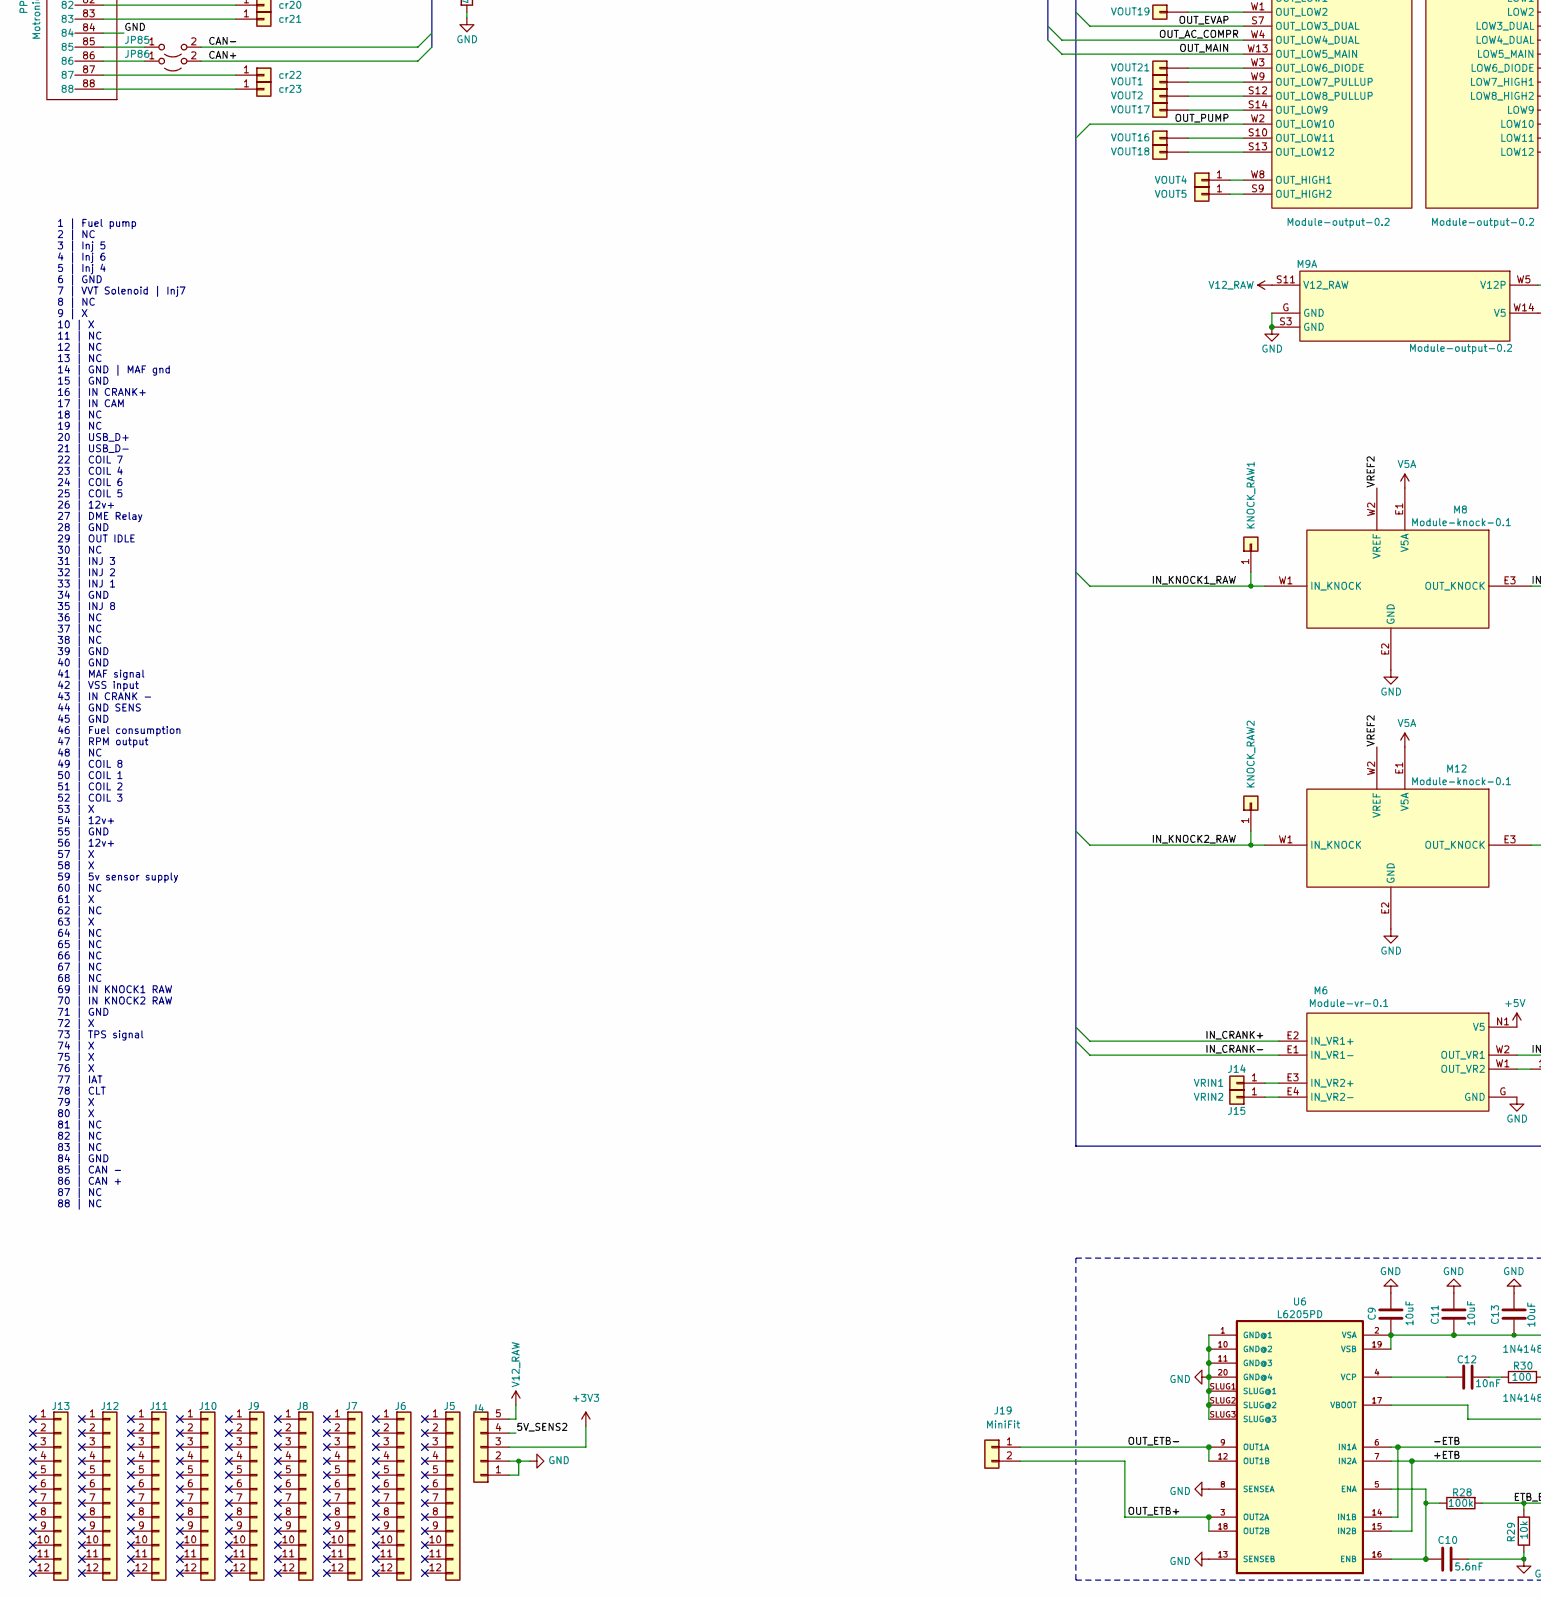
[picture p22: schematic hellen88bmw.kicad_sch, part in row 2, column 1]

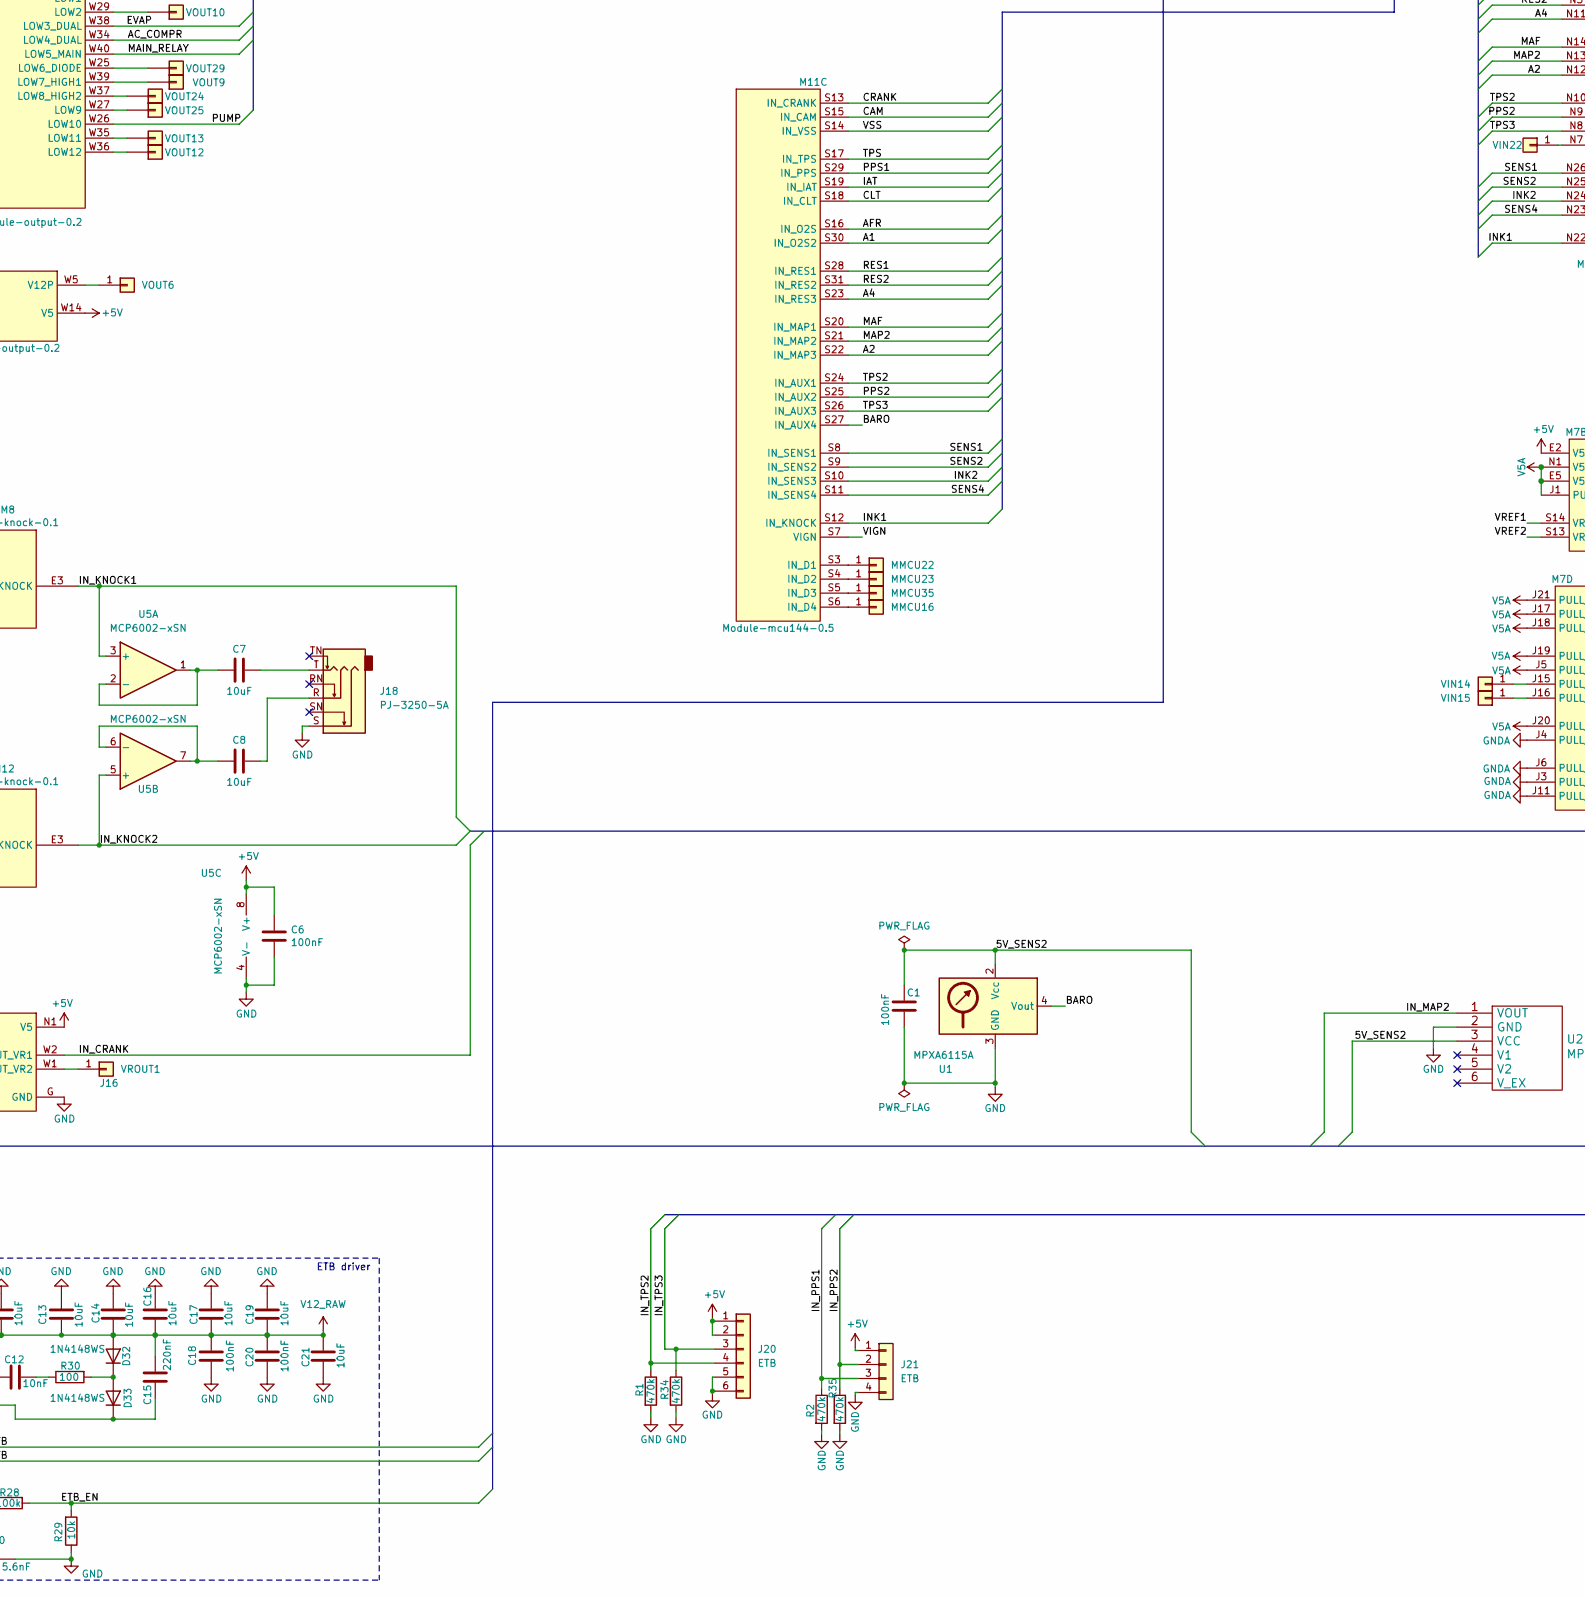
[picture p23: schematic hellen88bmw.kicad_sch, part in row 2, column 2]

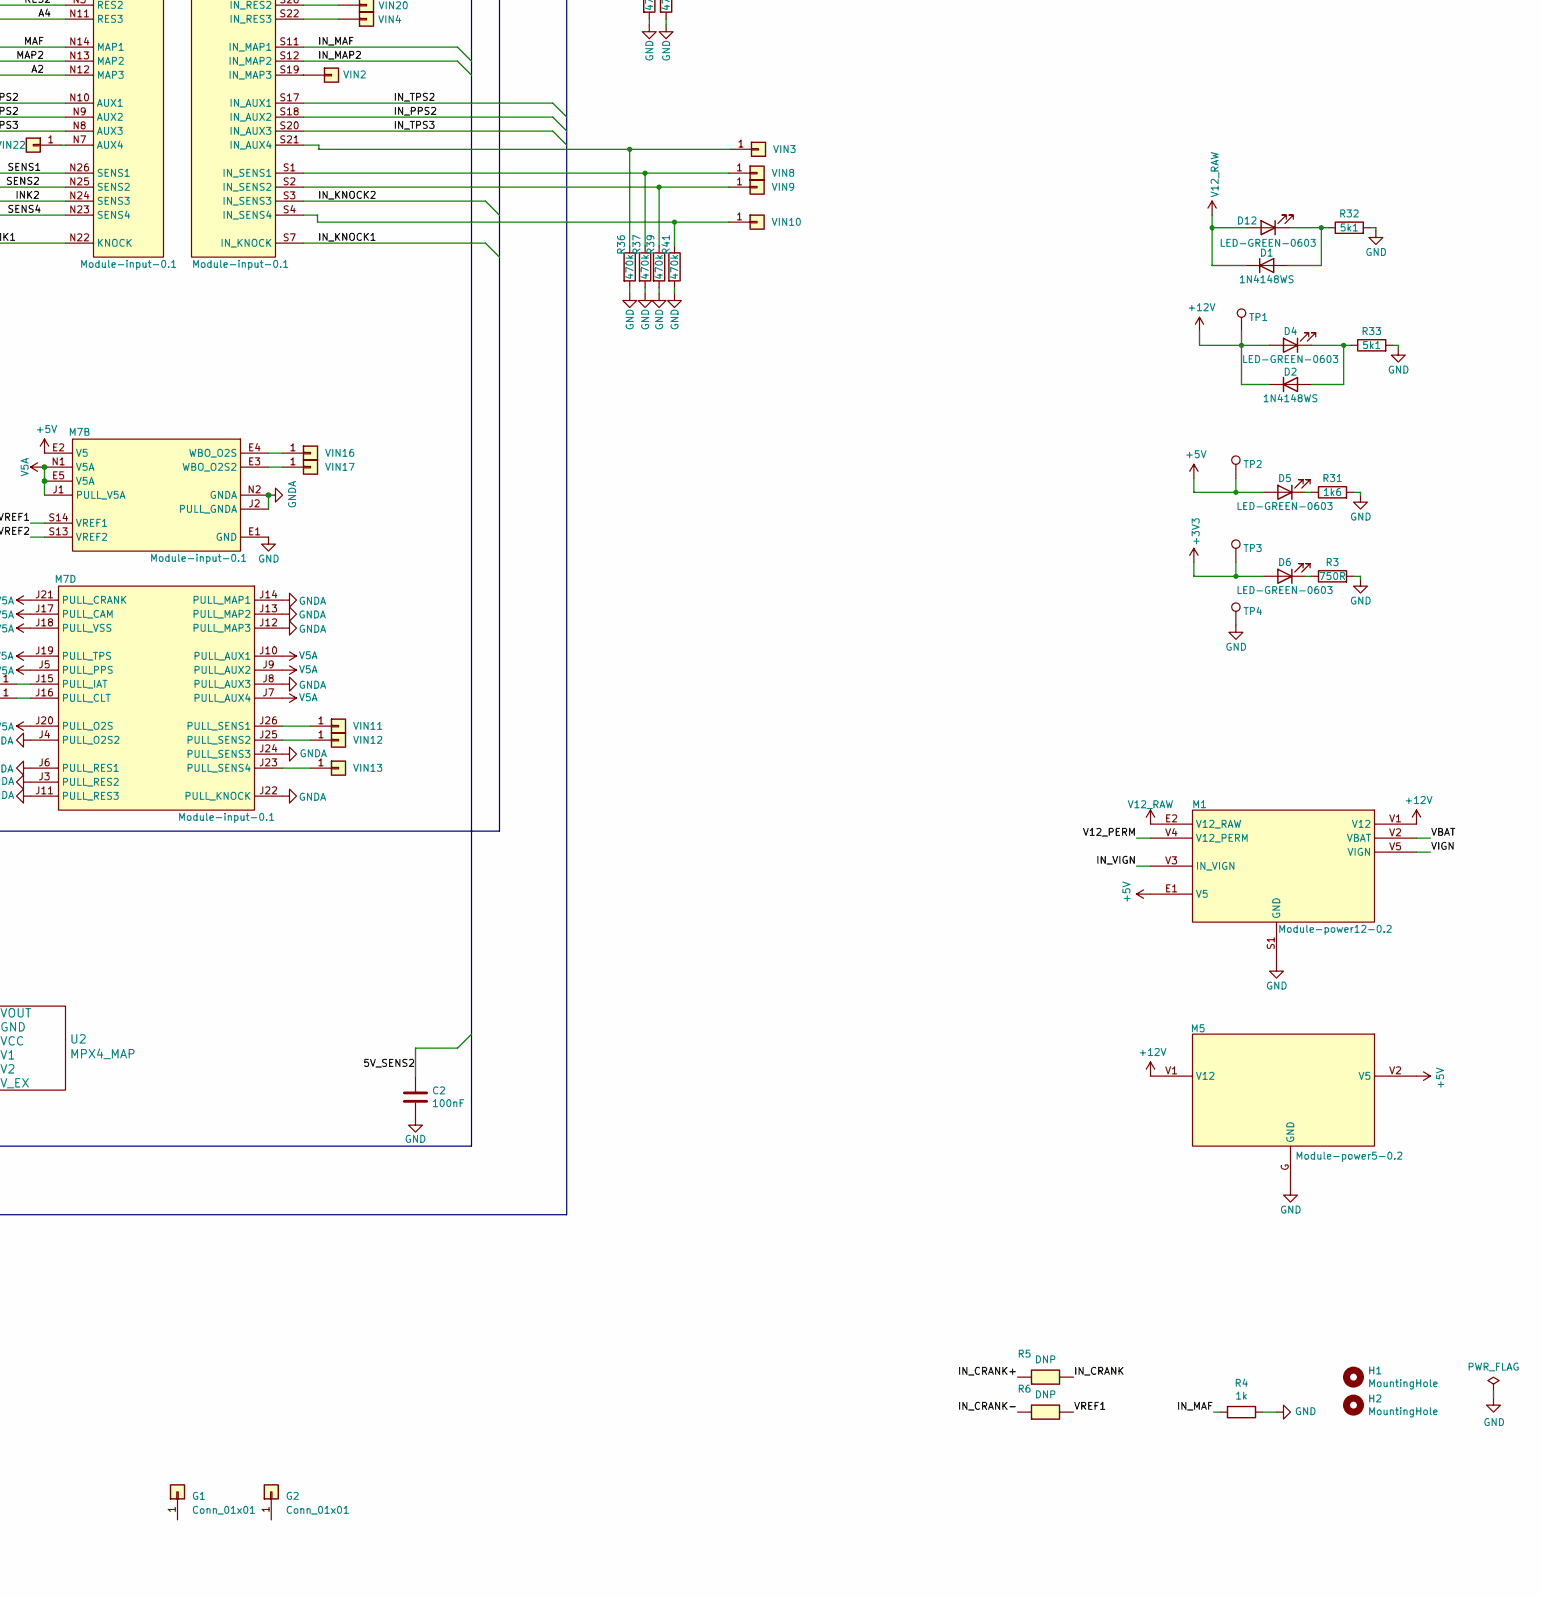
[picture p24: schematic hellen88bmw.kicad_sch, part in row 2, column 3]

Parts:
C1, C2, C3, C4, C5, C6, C18, C20, C22: 100nF; C_0402_1005Metric; LCSC C105882
C7, C8, C9, C11, C13, C14, C16, C17, C19, C21: 10uF; C_0603_1608Metric; LCSC C87152
C10: 5.6nF; C_0402_1005Metric; LCSC C115688
C12: 10nF; C_0402_1005Metric; LCSC C541443
C15: 220nF; C_0402_1005Metric; LCSC C106258
D1, D2, D3, D8, D10, D32, D33: 1N4148WS; D_SOD-323; LCSC C2128
D4, D5, D6, D12: LED-GREEN-0603; LED_0603_1608Metric; LCSC C72043
D7: LED-WHITE-0603; LED_0603_1608Metric; LCSC C84265
D9, D14, D16, D17, D18, D19, D20, D21, D22, D23: LED-BLUE-0603; LED_0603_1608Metric; LCSC C72041
D11, D15, D24, D25, D26, D27, D28, D29, D30, D31: LED-RED-0603; LED_0603_1608Metric; LCSC C2286
G1, G2: Conn_01x01; LOGO
H1, H2: MountingHole; MountingHole_4.3mm_M4_DIN965
J1: 920-462A2021Y10101; USB-MINI-B-VERTICAL; LCSC C13453
J2: UB-20PMFP-LC7002; PinHeader_1x05_P2.00mm_Vertical; LCSC DNP
J3: Micro_SD_Card; 693072010801
J4: Conn_01x05; PinHeader_1x05_P2.54mm_Vertical
J5, J6, J7, J8, J9, J10, J11, J12, J13: Conn_01x12; PinHeader_1x12_P2.54mm_Vertical
J14: VRIN1; PinHeader_1x01_P1.00mm_Vertical
J15: VRIN2; PinHeader_1x01_P1.00mm_Vertical
J16: VROUT1; PinHeader_1x01_P1.00mm_Vertical
J17: XH-8A; LCSC C10385
J18: PJ-3250-5A; Jack_3.5mm_CUI_SJ1-3535NG_Horizontal; LCSC C165947
J19: MiniFit; Molex_Mini-Fit_Jr_5569-02A2_2x01_P4.20mm_Horizontal
J20: ETB; PinHeader_1x06_P2.54mm_Vertical; LCSC C343639
J21: ETB; PinHeader_1x04_P2.54mm_Vertical; LCSC C343639
JP1, JP2, JP3, JP4, JP5, JP7, JP14, JP16, JP17, JP22, JP23, JP24, JP25, JP26, JP27, JP29, JP31, JP32, JP33, JP35, JP36, JP41, JP42, JP43, JP46, JP47, JP48, JP49, JP50, JP51, JP52, JP56, JP59, JP73, JP77, JP78, JP85, JP86: Jumper_2_Open; SM0805_jumper; LCSC C17477
JP6, JP20, JP21, JP54: Jumper_2_Open; SM0805_jumper; LCSC DNP
KNOCK_RAW1: IN_KNOCK1_RAW; PinHeader_1x01_P1.00mm_Vertical
KNOCK_RAW2: IN_KNOCK2_RAW; PinHeader_1x01_P1.00mm_Vertical
M1: Module-power12-0.2; power12
M2, M4: Module-can-0.1; can
M3: Module-wbo-0.2; wbo
M5: Module-power5-0.2; power5
M6: Module-vr-0.1; vr
M7: Module-input-0.1; input
M8, M12: Module-knock-0.1; knock
M9: Module-output-0.2; output
M10: Module-ign8-0.1; ign8
M11: Module-mcu144-0.5; mcu
MMCU1, MMCU2, MMCU3, MMCU4, MMCU5, MMCU6, MMCU7, MMCU8, MMCU9, MMCU10, MMCU11, MMCU12, MMCU13, MMCU14, MMCU15, MMCU16, MMCU18, MMCU21, MMCU22, MMCU23, MMCU24, MMCU25, MMCU26, MMCU27, MMCU28, MMCU29, MMCU30, MMCU31, MMCU32, MMCU35, MMCU38, MMCU40: MMCU; PinHeader_1x01_P1.00mm_Vertical
P1, P2, P3, P4, P5, P6: P; Pin_D1.0mm_L10.0mm
PP1: Motronic_88pin; 88pin_STS
Q1, Q2, Q3, Q4, Q5, Q6, Q7, Q8: NGD8201AN; TO-252-2; LCSC C151649
R1, R2, R27, R34, R35, R36, R37, R38, R39, R40, R41: 470k; R_0402_1005Metric
R3: 750R; R_0402_1005Metric
R4: 1k; R_0402_1005Metric; LCSC C105637
R5, R6: DNP; R_0402_1005Metric; LCSC NA
R7, R8, R9, R10, R11, R12, R13, R14: DNP; R_2512_6332Metric; LCSC NA
R15, R16: 4k7; R_0402_1005Metric; LCSC C163826
R17, R18, R19, R20, R21, R22, R23, R24: 0; R_0402_1005Metric; LCSC C106231
R25, R26: 2k7; R_0402_1005Metric; LCSC C138017
R28: 100k; R_0402_1005Metric; LCSC C106234
R29: 10k; R_0402_1005Metric; LCSC C60489
R30: 100; R_0402_1005Metric; LCSC C106233
R31: 1k6; R_0402_1005Metric
R32, R33: 5k1; R_0402_1005Metric
RN3, RN4, RN5, RN6, RN7, RN8: 470; R_Array_Concave_4x0603; LCSC C25510
SW1, SW2: RESET; SW_SPST_B3U-1000P-B; LCSC C231329
TP1, TP2, TP3, TP4: TestPoint; TestPoint_Pad_D1.0mm
U1: MPXA6115A; SSO-8_6.8x5.9mm_P1.27mm_Clearance7mm
U2: MPX4_MAP; MPX-4_MAP
U3: LIS2DW12TR; LGA12R50P4X4_200X200X70; PARTREV 4; LCSC C189624
U4: LPS25HB; ST_HLGA-10_2.5x2.5mm_P0.6mm_LayoutBorder3x2y; LCSC C87898
U5: MCP6002-xSN; SOIC-8_3.9x4.9mm_P1.27mm; LCSC C7377
U6: L6205PD; SO20POWER; LCSC C36543
VIN1, VIN2, VIN4, VIN18, VIN19, VIN20: Pad; PinHeader_1x01_P1.00mm_Vertical
VIN3, VIN8: VIN8; PinHeader_1x01_P1.00mm_Vertical
VIN9: VIN9; PinHeader_1x01_P1.00mm_Vertical
VIN10: VIN10; PinHeader_1x01_P1.00mm_Vertical
VIN11: VIN11; PinHeader_1x01_P1.00mm_Vertical
VIN12: VIN12; PinHeader_1x01_P1.00mm_Vertical
VIN13: VIN13; PinHeader_1x01_P1.00mm_Vertical
VIN14: VIN14; PinHeader_1x01_P1.00mm_Vertical
VIN15: VIN15; PinHeader_1x01_P1.00mm_Vertical
VIN16: VIN16; PinHeader_1x01_P1.00mm_Vertical
VIN17: VIN17; PinHeader_1x01_P1.00mm_Vertical
VIN22: VIN5; PinHeader_1x01_P1.00mm_Vertical
VOUT1, VOUT2, VOUT8, VOUT9, VOUT10, VOUT12, VOUT13, VOUT16, VOUT17, VOUT18, VOUT19, VOUT21, VOUT24, VOUT25, VOUT26, VOUT27, VOUT28, VOUT29: Pad; PinHeader_1x01_P1.00mm_Vertical
VOUT4, VOUT14, VOUT15, VOUT22, VOUT23: VOUT4; PinHeader_1x01_P1.00mm_Vertical
VOUT5: VOUT5; PinHeader_1x01_P1.00mm_Vertical
VOUT6: VOUT6; PinHeader_1x01_P1.00mm_Vertical
cr1, cr2, cr3, cr4, cr5, cr6, cr7, cr8, cr10, cr11, cr12, cr13, cr14, cr15, cr16, cr17, cr18, cr19, cr20, cr21, cr22, cr23: cr; PinHeader_1x01_P1.00mm_Vertical

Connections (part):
+3V3: C4.1, C5.1, C22.1, D6.2 (A), J3.4 (VDD), J4.3, M11.N16 (V33), R15.1, R16.1, SW1.2 (B), TP3.1, U3.9 (VDD), U3.10 (VDD_IO), U4.1 (VDDio), U4.6 (~CS), U4.10 (VDD)
+5V: C6.1, D5.2 (A), J20.1, J20.2, J21.1, M1.E1 (V5), M2.V1 (V5), M3.W1 (V5_IN), M4.V1 (V5), M5.V2 (V5), M6.N1 (V5), M7.E2 (V5), M9.W14 (V5), M11.S1 (V5), R25.1, R26.1, TP2.1, U5.8 (V+)
+12V: D2.1 (K), D3.1 (K), D4.2 (A), D8.1 (K), D10.1 (K), M1.V1 (V12), M5.V1 (V12), TP1.1
/5V_SENS2: C1.1, C2.1, J4.4, JP59.2 (B), U1.2 (Vcc), U2.3 (VCC)
/+ETB: M11.E14 (OUT_PWM2), U6.7 (IN2A), U6.15 (IN2B)
/-ETB: M11.E15 (OUT_PWM3), U6.6 (IN1A), U6.14 (IN1B)
/A1: M7.N4 (O2S2), M11.S30 (IN_O2S2)
/A2: M7.N12 (MAP3), M11.S22 (IN_MAP3)
/A4: M7.N11 (RES3), M11.S23 (IN_RES3)
/AC_COMPR: M9.W34 (LOW4_DUAL), M11.E21 (OUT_IO7)
/AFR: M7.N18 (O2S), M11.S16 (IN_O2S)
/BARO: M11.S27 (IN_AUX4), U1.4 (Vout)
/BOOT0: M11.N28 (BOOT0), SW1.1 (A)
/CAM: M7.N19 (CAM), M11.S15 (IN_CAM)
/CAN+: JP86.2 (B), M2.S2 (CANH), M4.S2 (CANH)
/CAN-: JP85.2 (B), M2.S1 (CANL), M4.S1 (CANL)
/CAN_RX: M2.V6 (CAN_RX), M11.N2 (CAN_RX)
/CAN_TX: M2.V5 (CAN_TX), M11.N3 (CAN_TX)
/CAN_VIO: M2.V2 (CAN_VIO), M11.N1 (CAN_VIO)
/CLT: M7.N16 (CLT), M11.S18 (IN_CLT)
/COIL_1: JP50.2 (B), Q1.2 (C), R7.1
/COIL_2: JP51.2 (B), Q3.2 (C), R9.1
/COIL_3: JP52.2 (B), Q5.2 (C), R12.2
/COIL_4: JP23.2 (B), Q2.2 (C), R8.1
/COIL_5: JP25.2 (B), Q6.2 (C), R11.2
/COIL_6: JP24.2 (B), Q4.2 (C), R13.2
/COIL_7: JP22.2 (B), Q7.2 (C), R10.1
/COIL_8: JP49.2 (B), Q8.2 (C), R14.2
/CRANK: M7.N21 (CRANK), M11.S13 (IN_CRANK)
/ETB_EN: M11.E27 (OUT_PWM1), R28.2, R29.2
/EVAP: M9.W38 (LOW3_DUAL), M11.E7 (OUT_IO5)
/FUEL_CONSUM: M9.W22 (PP2), M11.E18 (OUT_PWM6)
/IAT: M7.N15 (IAT), M11.S19 (IN_IAT)
/IDLE: M9.W21 (LOW1), M11.E17 (OUT_PWM5)
/IGN1: M10.V8 (IGN1), M11.W1 (OUT_IGN1)
/IGN2: M10.V7 (IGN2), M11.W2 (OUT_IGN2)
/IGN3: M10.V6 (IGN3), M11.W3 (OUT_IGN3)
/IGN4: M10.V5 (IGN4), M11.W4 (OUT_IGN4)
/IGN5: M10.V4 (IGN5), M11.W5 (OUT_IGN5)
/IGN6: M10.V3 (IGN6), M11.W6 (OUT_IGN6)
/IGN7: M10.V2 (IGN7), M11.W7 (OUT_IGN7)
/IGN8: M10.V1 (IGN8), M11.W8 (OUT_IGN8)
/IGN_V5: M10.V9 (VCC), M11.W9 (IGN_V5)
/IGN_V33: M10.V10 (V33), M11.W10 (IGN_V33)
/INJ1: D24.2 (A), M9.W24 (INJ1), M11.E25 (OUT_INJ1)
/INJ2: D28.2 (A), M9.W23 (INJ2), M11.E26 (OUT_INJ2)
/INJ3: D25.2 (A), M9.W20 (INJ3), M11.E29 (OUT_INJ3)
/INJ4: D29.2 (A), M9.W19 (INJ4), M11.E30 (OUT_INJ4)
/INJ5: D26.2 (A), M9.W18 (INJ5), M11.E31 (OUT_INJ5)
/INJ6: D30.2 (A), M9.W17 (INJ6), M11.E32 (OUT_INJ6)
/INJ7: D27.2 (A), M9.W16 (INJ7), M11.E33 (OUT_INJ7)
/INJ8: D31.2 (A), M9.W15 (INJ8), M11.E34 (OUT_INJ8)
/INK1: M7.N22 (KNOCK), M11.S12 (IN_KNOCK)
/INK2: M7.N24 (SENS3), M11.S10 (IN_SENS3)
/IN_CAM: JP17.2 (B), M7.S5 (IN_CAM)
/IN_CLT: JP78.2 (B), M7.S15 (IN_CLT), R25.2
/IN_CRANK: D7.2 (A), M6.W2 (OUT_VR1), M7.S8 (IN_CRANK), R5.2
/IN_CRANK+: JP16.2 (B), M6.E2 (IN_VR1+), R5.1
/IN_CRANK-: JP43.2 (B), M6.E1 (IN_VR1-), R6.1
/IN_IAT: JP77.2 (B), M7.S16 (IN_IAT), R26.2
/IN_KNOCK1: M7.S7 (IN_KNOCK), M8.E3 (OUT_KNOCK), U5.3 (+)
/IN_KNOCK1_RAW: KNOCK_RAW1.1, M8.W1 (IN_KNOCK), PP1.69
/IN_KNOCK2: M7.S3 (IN_SENS3), M12.E3 (OUT_KNOCK), U5.5 (+)
/IN_KNOCK2_RAW: KNOCK_RAW2.1, M12.W1 (IN_KNOCK), PP1.70
/IN_MAF: JP14.2 (B), JP41.2 (B), M7.S11 (IN_MAP1), R4.2
/IN_MAP2: M7.S12 (IN_MAP2), U2.1 (VOUT)
/IN_PPS1: J21.3, M7.S24 (IN_PPS), R2.1
/IN_PPS2: J21.2, M7.S18 (IN_AUX2), R35.1
/IN_TPS: JP73.2 (B), M7.S10 (IN_TPS), R27.1
/IN_TPS2: J20.4, M7.S17 (IN_AUX1), R1.1
/IN_TPS3: J20.3, M7.S20 (IN_AUX3), R34.1
/IN_VIGN: JP2.2 (B), M1.V3 (IN_VIGN)
/IN_VSS: JP42.2 (B), M7.S6 (IN_VSS)
/LPS_SCL: M11.N19 (I2C_SCL), R16.2, U4.2 (SCL/SCLK)
/LPS_SDA: M11.N18 (I2C_SDA), R15.2, U4.4 (SDA/MOSI)
/LSU_CALIBR_RES: J17.5, M3.E4 (LSU_Rtrim), P3.1
/LSU_HEAT-: J17.3, J17.4, M3.E5 (LSU_H+), P2.1
/LSU_PUMP_I: J17.6, M3.E3 (LSU_Ip), P4.1
/LSU_SENSOR_U: J17.8, M3.E1 (LSU_Un), P6.1
/LSU_SENSOR_U/PUMP_I: J17.7, M3.E2 (LSU_Vm), P5.1
/MAF: M7.N14 (MAP1), M11.S20 (IN_MAP1)
/MAIN_RELAY: D11.2 (A), M9.W40 (LOW5_MAIN), M11.E8 (OUT_IO1)
/MAP2: M7.N13 (MAP2), M11.S21 (IN_MAP2)
/NRESET: C3.1, M11.N24 (nReset), SW2.1 (A)
/OUT_AC_COMPR: JP48.2 (B), M9.W4 (OUT_LOW4_DUAL)
/OUT_ETB+: J19.2, U6.3 (OUT2A), U6.18 (OUT2B)
/OUT_ETB-: J19.1, U6.9 (OUT1A), U6.12 (OUT1B)
/OUT_EVAP: D8.2 (A), JP36.2 (B), M9.S7 (OUT_LOW3_DUAL)
/OUT_FUEL_CONSUM: JP46.2 (B), M9.S6 (OUT_PP2)
/OUT_IDLE: D10.2 (A), D14.2 (A), JP29.2 (B), M9.S8 (OUT_LOW1)
/OUT_IGN1: D23.2 (A), M10.S8 (OUT_IGN1), R7.2, R17.1
/OUT_IGN2: D19.2 (A), M10.S7 (OUT_IGN2), R9.2, R19.1
/OUT_IGN3: D22.2 (A), M10.S6 (OUT_IGN3), R12.1, R22.2
/OUT_IGN4: D18.2 (A), M10.S5 (OUT_IGN4), R8.2, R18.1
/OUT_IGN5: D21.2 (A), M10.S4 (OUT_IGN5), R11.1, R21.2
/OUT_IGN6: D17.2 (A), M10.S3 (OUT_IGN6), R13.1, R23.2
/OUT_IGN7: D20.2 (A), M10.S2 (OUT_IGN7), R10.2, R20.1
/OUT_IGN8: D16.2 (A), M10.S1 (OUT_IGN8), R14.1, R24.2
/OUT_INJ1: JP33.2 (B), M9.S18 (OUT_INJ1)
/OUT_INJ2: JP32.2 (B), M9.S16 (OUT_INJ2)
/OUT_INJ3: JP31.2 (B), M9.S17 (OUT_INJ3)
/OUT_INJ4: JP5.2 (B), M9.W7 (OUT_INJ4)
/OUT_INJ5: JP3.2 (B), M9.W10 (OUT_INJ5)
/OUT_INJ6: JP4.2 (B), M9.S15 (OUT_INJ6)
/OUT_INJ7: JP6.1 (A), JP7.2 (B), M9.W12 (OUT_INJ7)
/OUT_INJ8: JP35.2 (B), M9.W11 (OUT_INJ8)
/OUT_MAIN: JP27.2 (B), M9.W13 (OUT_LOW5_MAIN)
/OUT_PUMP: D15.2 (A), JP1.2 (B), M9.W2 (OUT_LOW10)
/OUT_TACH: JP47.2 (B), M9.W6 (OUT_PP1)
/PPS1: M7.N5 (PPS), M11.S29 (IN_PPS)
/PPS2: M7.N9 (AUX2), M11.S25 (IN_AUX2)
/PUMP: D9.2 (A), M9.W26 (LOW10), M11.E6 (OUT_IO3)
/RES1: M7.N6 (RES1), M11.S28 (IN_RES1)
/RES2: M7.N3 (RES2), M11.S31 (IN_RES2)
/SD_CLK: J3.5 (CLK), M11.N9 (SPI3_SCK)
/SD_CS: J3.2 (DAT3/CD), M11.N8 (SPI3_CS)
/SD_MISO: J3.7 (DAT0), M11.N10 (SPI3_MISO)
/SD_MOSI: J3.3 (CMD), M11.N11 (SPI3_MOSI)
/SENS1: M7.N26 (SENS1), M11.S8 (IN_SENS1)
/SENS2: M7.N25 (SENS2), M11.S9 (IN_SENS2)
/SENS4: M7.N23 (SENS4), M11.S11 (IN_SENS4)
/SPI_CS: M11.N23 (SPI2_CS), U3.2 (CS)
/SPI_MISO: M11.N21 (SPI2_MISO), U3.3 (SDO/SDA0)
/SPI_MOSI: M11.N22 (SPI2_MOSI), U3.4 (SDA/SDI/SDO)
/SPI_SCK: M11.N20 (SPI2_SCK), U3.1 (SCL/SPC)
/TACH: M9.W28 (PP1), M11.E19 (OUT_PWM7)
/TPS: M7.N17 (TPS), M11.S17 (IN_TPS)
/TPS2: M7.N10 (AUX1), M11.S24 (IN_AUX1)
/TPS3: M7.N8 (AUX3), M11.S26 (IN_AUX3)
/USBM: J1.2 (D-), J2.2 (D-), JP21.2 (B), M11.N31 (USB1M)
/USBP: J1.3 (D+), J2.3 (D+), JP20.2 (B), M11.N30 (USB1P)
/V12_PERM: JP26.2 (B), M1.V4 (V12_PERM)
/VBAT: M1.V2 (VBAT), M11.N17 (VBAT)
/VBUS: J1.1 (VBUS), J2.1 (VBUS), M11.N29 (VBUS)
/VIGN: M1.V5 (VIGN), M11.S7 (VIGN)
/VREF1: M7.S14 (VREF1), R6.2
/VREF2: M7.S13 (VREF2), M8.W2 (VREF), M12.W2 (VREF)
/VSS: M7.N20 (VSS), M11.S14 (IN_VSS)
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

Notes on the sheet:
1 | Fuel pump 2 | NC 3 | Inj 5 4 | Inj 6 5 | Inj 4 6 | GND 7 | VVT Solenoid | Inj7 8 | NC 9 | X 10 | X 11 | NC 12 | NC 13 | NC 14 | GND | MAF gnd 15 | GND 16 | IN CRANK+ 17 | IN CAM 18 | NC 19 | NC 20 | USB_D+ 21 | USB_D- 22 | COIL 7 23 | COIL 4 24 | COIL 6 25 | COIL 5 26 | 12v+ 27 | DME Relay 28 |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
ETB driver

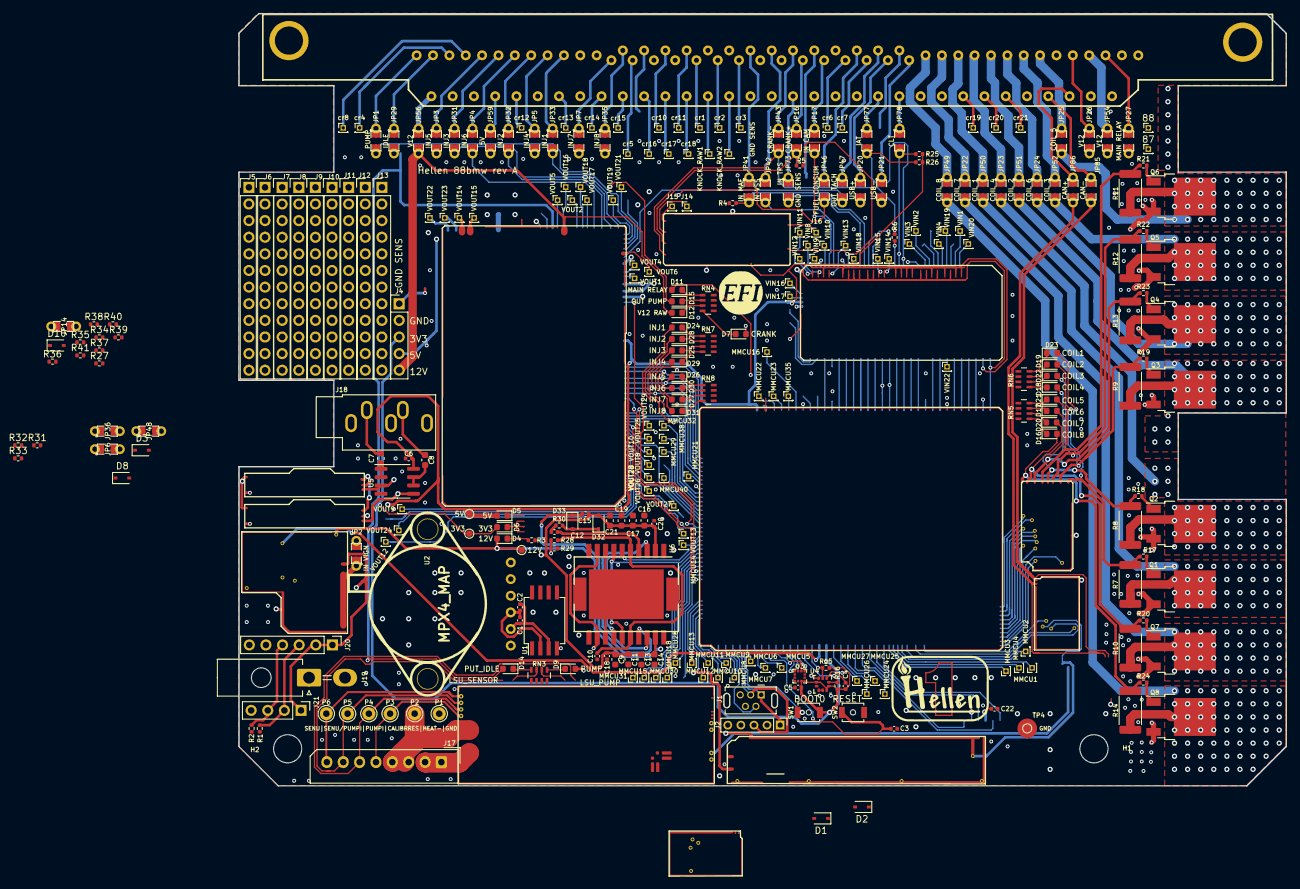
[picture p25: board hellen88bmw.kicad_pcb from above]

Board: 4 copper layers, 160.0 x 118.0 mm, 306 parts (1 on the bottom side), 328 nets.

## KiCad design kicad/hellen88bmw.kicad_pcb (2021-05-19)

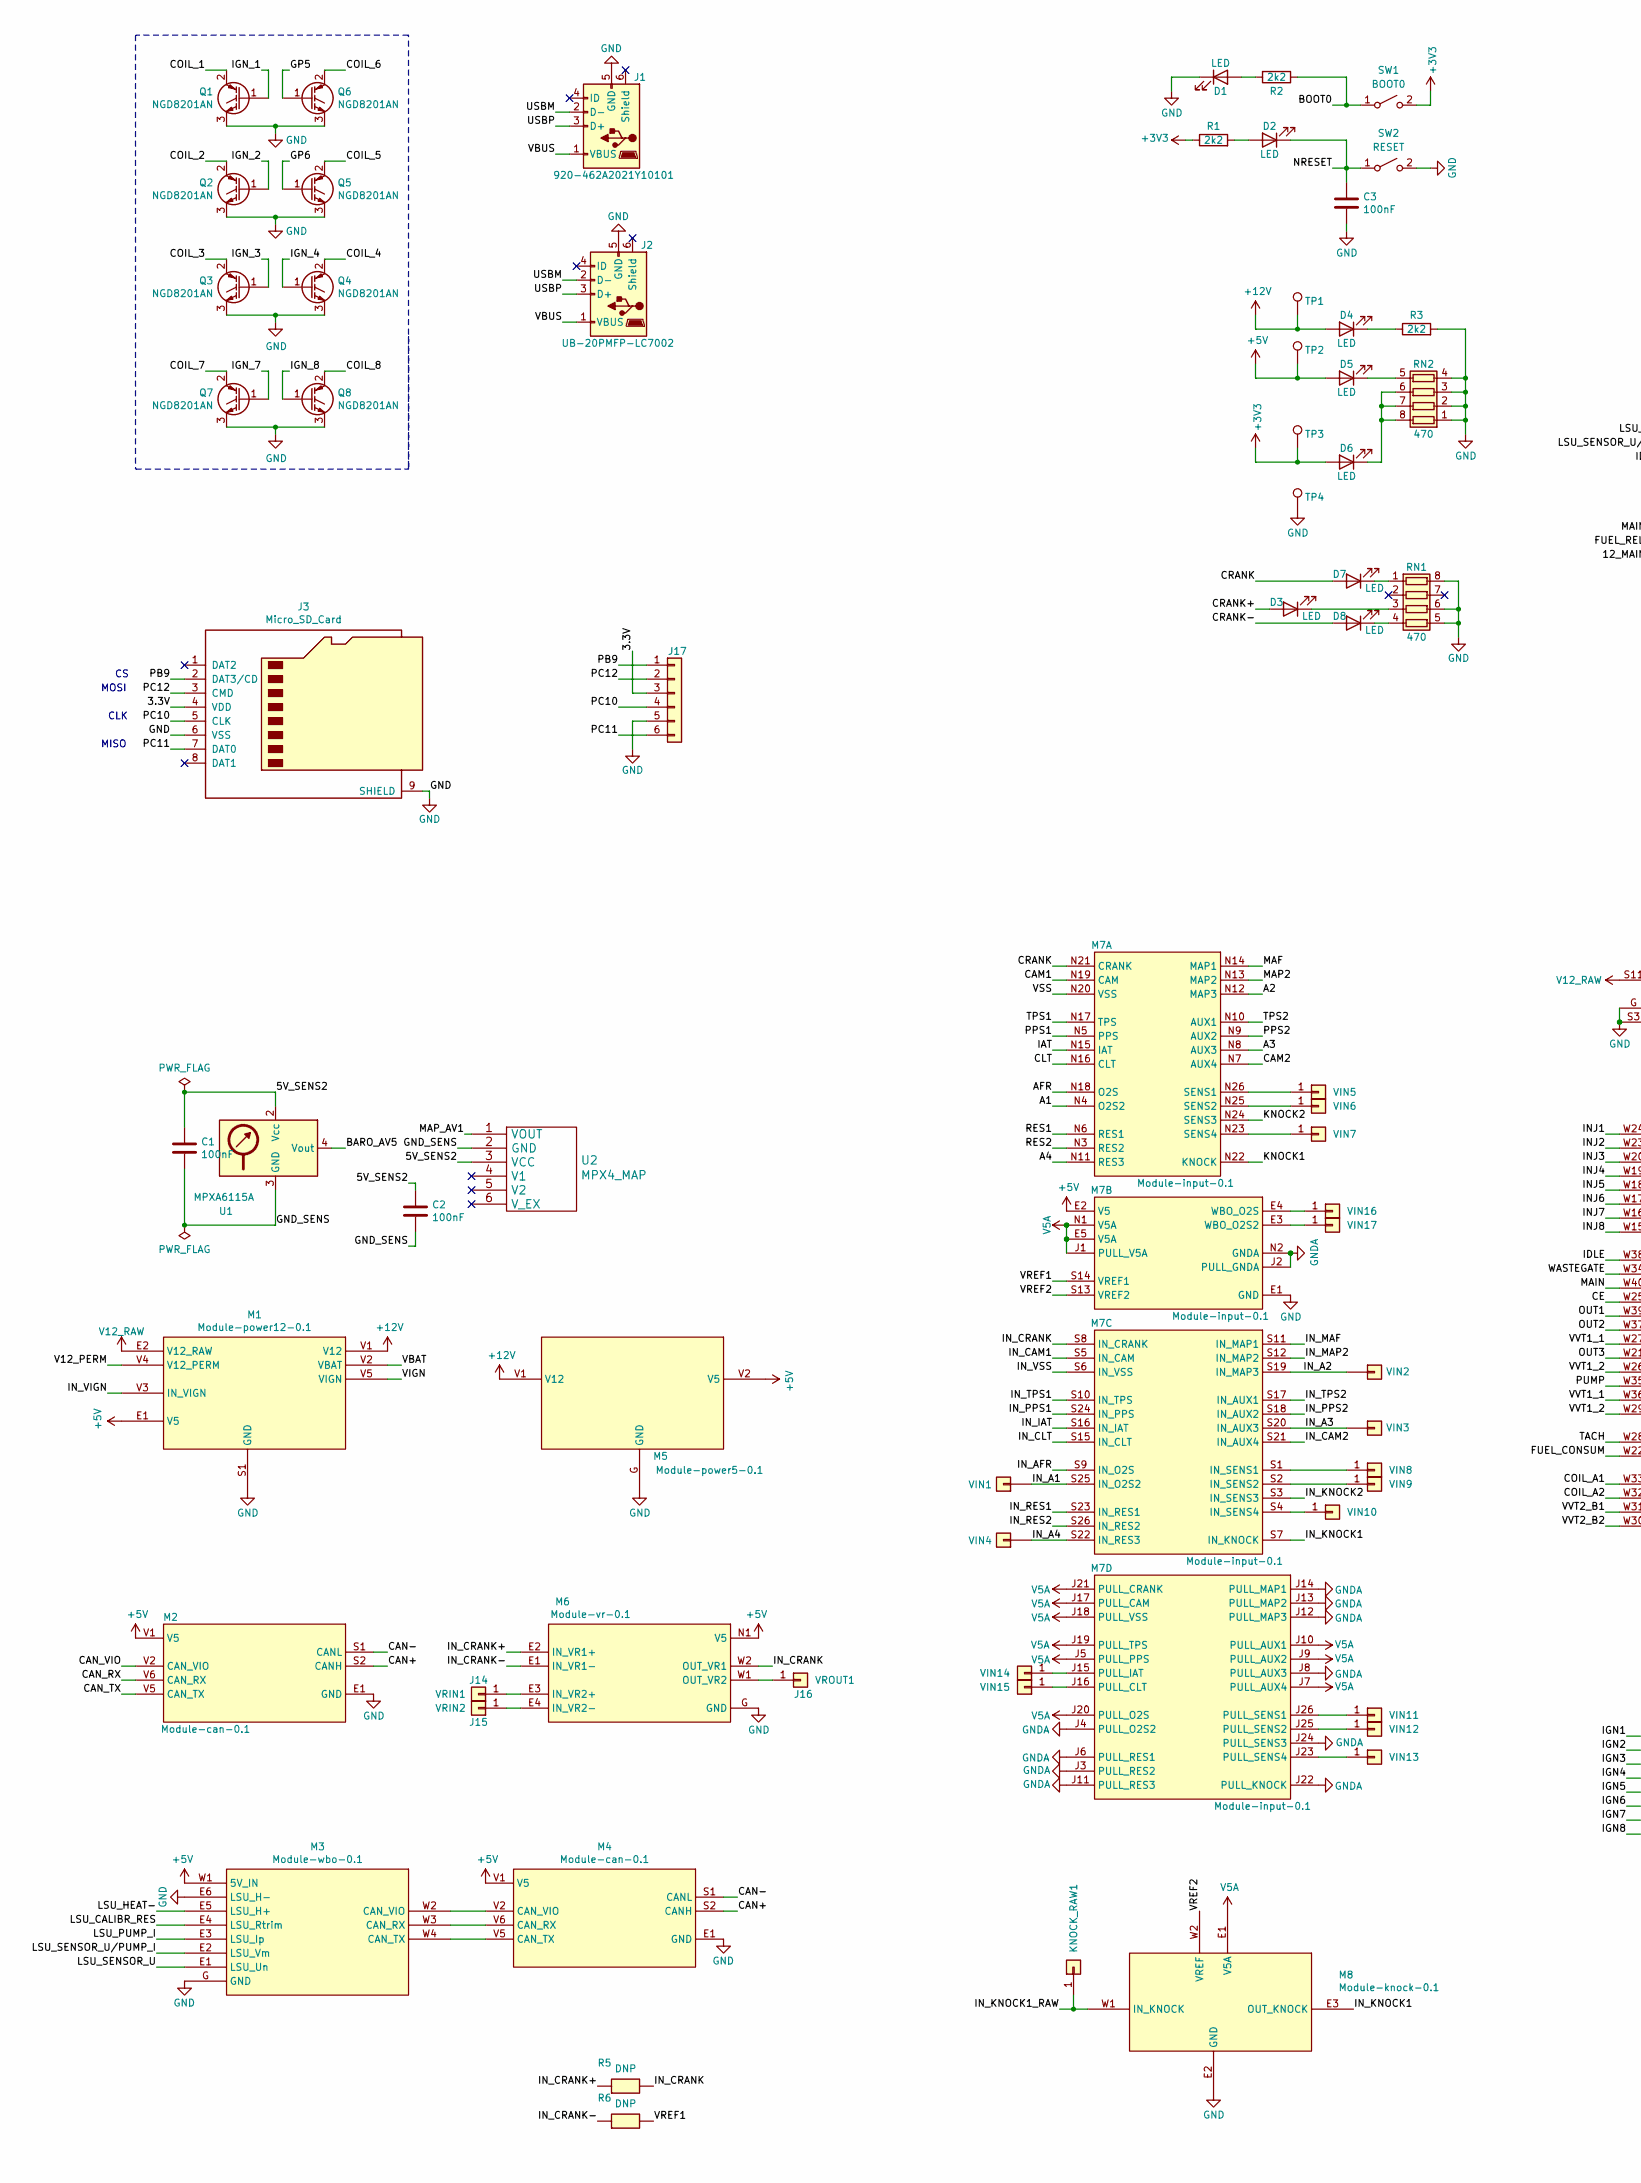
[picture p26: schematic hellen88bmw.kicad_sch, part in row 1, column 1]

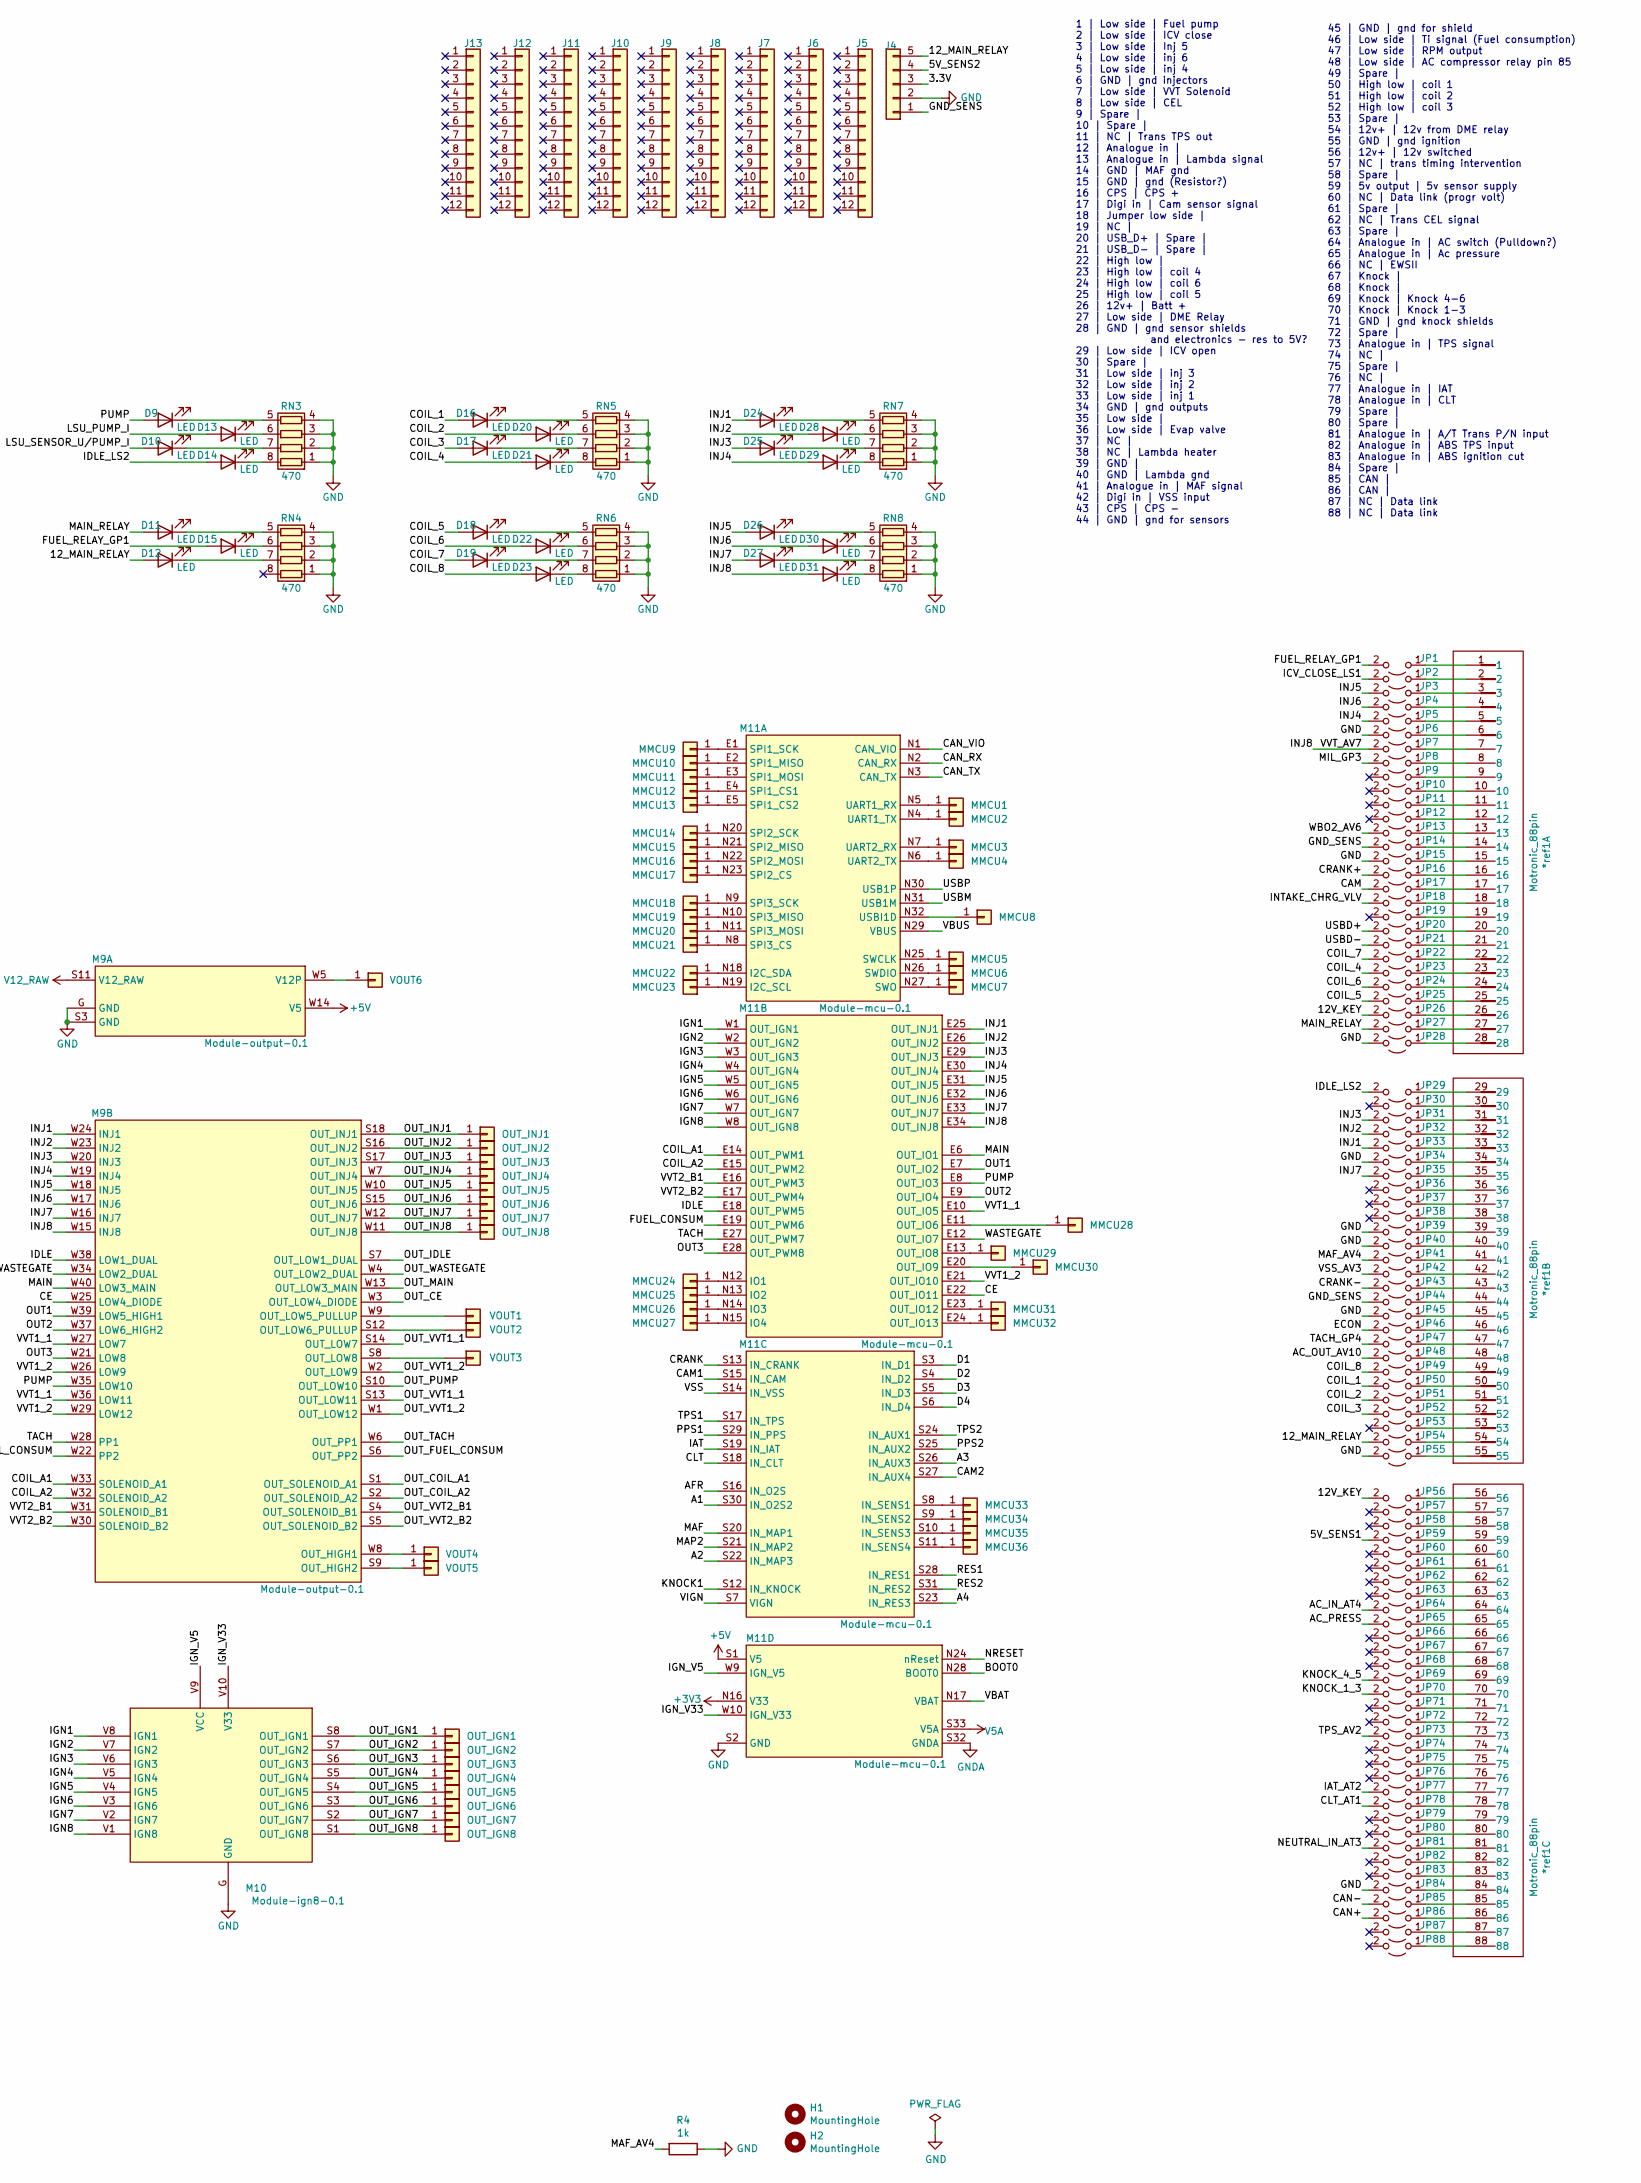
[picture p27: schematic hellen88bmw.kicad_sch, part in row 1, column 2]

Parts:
*ref1: Motronic_88pin; 88pin_STS
C1, C2, C3: 100nF; C_0603_1608Metric; LCSC C49678
D1, D2, D3, D4, D5, D6, D7, D8, D9, D10, D11, D12, D13, D14, D15, D16, D17, D18, D19, D20, D21, D22, D23, D24, D25, D26, D27, D28, D29, D30, D31: LED; LED_0603_1608Metric
H1, H2: MountingHole; MountingHole_4.3mm_M4_DIN965
J1: 920-462A2021Y10101; USB-MINI-B-VERTICAL; LCSC C13453
J2: UB-20PMFP-LC7002; PinHeader_1x05_P2.00mm_Vertical; LCSC C13453
J3: Micro_SD_Card; 693072010801
J4: Conn_01x05; PinHeader_1x05_P2.54mm_Vertical
J5, J6, J7, J8, J9, J10, J11, J12, J13: Conn_01x12; PinHeader_1x12_P2.54mm_Vertical
J14: VRIN1; PinHeader_1x01_P1.00mm_Vertical
J15: VRIN2; PinHeader_1x01_P1.00mm_Vertical
J16: VROUT1; PinHeader_1x01_P1.00mm_Vertical
J17: SD; PinHeader_1x06_P2.54mm_Vertical
JP1: Jumper_2_Open; SM0805_jumper; LCSC C17477
JP2, JP3, JP4, JP5, JP6, JP7, JP8, JP9, JP10, JP11, JP12, JP13, JP14, JP15, JP16, JP17, JP18, JP19, JP20, JP21, JP22, JP23, JP24, JP25, JP26, JP27, JP28, JP29, JP30, JP31, JP32, JP33, JP34, JP35, JP36, JP37, JP38, JP39, JP40, JP41, JP42, JP43, JP44, JP45, JP46, JP47, JP48, JP49, JP50, JP51, JP52, JP53, JP54, JP55, JP56, JP57, JP58, JP59, JP60, JP61, JP62, JP63, JP64, JP65, JP66, JP67, JP68, JP69, JP70, JP71, JP72, JP73, JP74, JP75, JP76, JP77, JP78, JP79, JP80, JP81, JP82, JP83, JP84, JP85, JP86, JP87, JP88: Jumper_2_Open; SM0805_jumper
KNOCK_RAW1: IN_KNOCK1_RAW; PinHeader_1x01_P1.00mm_Vertical
M1: Module-power12-0.1; MOD_HELLEN_POWER_12
M2, M4: Module-can-0.1; MOD_HELLEN_CAN
M3: Module-wbo-0.1; MOD_HELLEN_WBO
M5: Module-power5-0.1; MOD_HELLEN_POWER_5
M6: Module-vr-0.1; MOD_HELLEN_VR
M7: Module-input-0.1; MOD_HELLEN_INPUT
M8: Module-knock-0.1; MOD_HELLEN_KNOCK
M9: Module-output-0.1; MOD_HELLEN_OUTPUT
M10: Module-ign8-0.1; MOD_HELLEN_IGN8
M11: Module-mcu-0.1; MOD_HELLEN_MCU
MMCU1: MMCU1; PinHeader_1x01_P1.00mm_Vertical
MMCU2, MMCU3, MMCU4, MMCU5, MMCU6, MMCU7, MMCU8, MMCU9, MMCU10, MMCU11, MMCU12, MMCU13, MMCU14, MMCU15, MMCU16, MMCU17, MMCU18, MMCU19, MMCU20, MMCU21, MMCU22, MMCU23, MMCU24, MMCU25, MMCU26, MMCU27, MMCU28, MMCU29, MMCU30, MMCU31, MMCU32, MMCU33, MMCU34, MMCU35, MMCU36: MMCU; PinHeader_1x01_P1.00mm_Vertical
OUT_IGN1: OUT_IGN1; PinHeader_1x01_P1.00mm_Vertical
OUT_IGN2: OUT_IGN2; PinHeader_1x01_P1.00mm_Vertical
OUT_IGN3: OUT_IGN3; PinHeader_1x01_P1.00mm_Vertical
OUT_IGN4: OUT_IGN4; PinHeader_1x01_P1.00mm_Vertical
OUT_IGN5: OUT_IGN5; PinHeader_1x01_P1.00mm_Vertical
OUT_IGN6: OUT_IGN6; PinHeader_1x01_P1.00mm_Vertical
OUT_IGN7: OUT_IGN7; PinHeader_1x01_P1.00mm_Vertical
OUT_IGN8: OUT_IGN8; PinHeader_1x01_P1.00mm_Vertical
OUT_INJ1: OUT_INJ1; PinHeader_1x01_P1.00mm_Vertical
OUT_INJ2: OUT_INJ2; PinHeader_1x01_P1.00mm_Vertical
OUT_INJ3: OUT_INJ3; PinHeader_1x01_P1.00mm_Vertical
OUT_INJ4: OUT_INJ4; PinHeader_1x01_P1.00mm_Vertical
OUT_INJ5: OUT_INJ5; PinHeader_1x01_P1.00mm_Vertical
OUT_INJ6: OUT_INJ6; PinHeader_1x01_P1.00mm_Vertical
OUT_INJ7: OUT_INJ7; PinHeader_1x01_P1.00mm_Vertical
OUT_INJ8: OUT_INJ8; PinHeader_1x01_P1.00mm_Vertical
Q1, Q2, Q3, Q4, Q5, Q7, Q8: NGD8201AN; TO-252-2
Q6: NGD8201AN; TO-252-2; LCSC C151649
R1, R2, R3: 2k2; R_0603_1608Metric
R4: 1k; R_0603_1608Metric; LCSC C17513
R5, R6: DNP; R_0603_1608Metric
RN1, RN2, RN3, RN4, RN5, RN6, RN7, RN8: 470; R_Array_Concave_4x0603
SW1: BOOT0; SW_SPST_B3U-1000P-B
SW2: RESET; SW_SPST_B3U-1000P-B
TP1, TP2, TP3, TP4: TestPoint; TestPoint_Pad_D1.0mm
U1: MPXA6115A; SSO-8_6.8x5.9mm_P1.27mm_Clearance7mm
U2: MPX4_MAP; MPX-4_MAP
VIN1, VIN2, VIN3, VIN4: Pad; PinHeader_1x01_P1.00mm_Vertical
VIN5: VIN5; PinHeader_1x01_P1.00mm_Vertical
VIN6: VIN6; PinHeader_1x01_P1.00mm_Vertical
VIN7: VIN7; PinHeader_1x01_P1.00mm_Vertical
VIN8: VIN8; PinHeader_1x01_P1.00mm_Vertical
VIN9: VIN9; PinHeader_1x01_P1.00mm_Vertical
VIN10: VIN10; PinHeader_1x01_P1.00mm_Vertical
VIN11: VIN11; PinHeader_1x01_P1.00mm_Vertical
VIN12: VIN12; PinHeader_1x01_P1.00mm_Vertical
VIN13: VIN13; PinHeader_1x01_P1.00mm_Vertical
VIN14: VIN14; PinHeader_1x01_P1.00mm_Vertical
VIN15: VIN15; PinHeader_1x01_P1.00mm_Vertical
VIN16: VIN16; PinHeader_1x01_P1.00mm_Vertical
VIN17: VIN17; PinHeader_1x01_P1.00mm_Vertical
VOUT1, VOUT2, VOUT3: Pad; PinHeader_1x01_P1.00mm_Vertical
VOUT4: VOUT4; PinHeader_1x01_P1.00mm_Vertical
VOUT5: VOUT5; PinHeader_1x01_P1.00mm_Vertical
VOUT6: VOUT6; PinHeader_1x01_P1.00mm_Vertical

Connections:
+3V3: D6.2 (A), M11.N16 (V33), R1.1, SW1.2 (B), TP3.1
+5V: D5.2 (A), M1.E1 (V5), M2.V1 (V5), M3.W1 (5V_IN), M4.V1 (V5), M5.V2 (V5), M6.N1 (V5), M7.E2 (V5), M9.W14 (V5), M11.S1 (V5), TP2.1
+12V: D4.2 (A), M1.V1 (V12), M5.V1 (V12), TP1.1
/3.3V: J3.4 (VDD), J4.3, J17.3
/5V_SENS1: JP59.2 (B)
/5V_SENS2: C1.1, C2.1, J4.4, U1.2 (Vcc), U2.3 (VCC)
/12V_KEY: JP26.2 (B), JP56.2 (B)
/12_MAIN_RELAY: D12.2 (A), J4.5, JP54.2 (B)
/A1: M7.N4 (O2S2), M11.S30 (IN_O2S2)
/A2: M7.N12 (MAP3), M11.S22 (IN_MAP3)
/A3: M7.N8 (AUX3), M11.S26 (IN_AUX3)
/A4: M7.N11 (RES3), M11.S23 (IN_RES3)
/AC_IN_AT4: JP64.2 (B)
/AC_OUT_AV10: JP48.2 (B)
/AC_PRESS: JP65.2 (B)
/AFR: M7.N18 (O2S), M11.S16 (IN_O2S)
/BARO_AV5: U1.4 (Vout)
/BOOT0: M11.N28 (BOOT0), R2.1, SW1.1 (A)
/CAM: JP17.2 (B)
/CAM1: M7.N19 (CAM), M11.S15 (IN_CAM)
/CAM2: M7.N7 (AUX4), M11.S27 (IN_AUX4)
/CAN+: JP86.2 (B), M2.S2 (CANH), M4.S2 (CANH)
/CAN-: JP85.2 (B), M2.S1 (CANL), M4.S1 (CANL)
/CAN_RX: M2.V6 (CAN_RX), M11.N2 (CAN_RX)
/CAN_TX: M2.V5 (CAN_TX), M11.N3 (CAN_TX)
/CAN_VIO: M2.V2 (CAN_VIO), M11.N1 (CAN_VIO)
/CE: M9.W25 (LOW4_DIODE), M11.E22 (OUT_IO11)
/CLT: M7.N16 (CLT), M11.S18 (IN_CLT)
/CLT_AT1: JP78.2 (B)
/COIL_1: D16.2 (A), JP50.2 (B), Q1.2 (C)
/COIL_2: D20.2 (A), JP51.2 (B), Q2.2 (C)
/COIL_3: D17.2 (A), JP52.2 (B), Q3.2 (C)
/COIL_4: D21.2 (A), JP23.2 (B), Q4.2 (C)
/COIL_5: D18.2 (A), JP25.2 (B), Q5.2 (C)
/COIL_6: D22.2 (A), JP24.2 (B), Q6.2 (C)
/COIL_7: D19.2 (A), JP22.2 (B), Q7.2 (C)
/COIL_8: D23.2 (A), JP49.2 (B), Q8.2 (C)
/COIL_A1: M9.W33 (SOLENOID_A1), M11.E14 (OUT_PWM1)
/COIL_A2: M9.W32 (SOLENOID_A2), M11.E15 (OUT_PWM2)
/CRANK: D7.2 (A), M7.N21 (CRANK), M11.S13 (IN_CRANK)
/CRANK+: D3.2 (A), JP16.2 (B)
/CRANK-: D8.2 (A), JP43.2 (B)
/D1: M11.S3 (IN_D1)
/D2: M11.S4 (IN_D2)
/D3: M11.S5 (IN_D3)
/D4: M11.S6 (IN_D4)
/ECON: JP46.2 (B)
/FUEL_CONSUM: M9.W22 (PP2), M11.E19 (OUT_PWM6)
/FUEL_RELAY_GP1: D15.2 (A), JP1.2 (B)
/GND_SENS: C1.2, C2.2, J4.1, JP14.2 (B), JP44.2 (B), U1.3 (GND), U2.2 (GND)
/GP5: Q6.1 (G)
/GP6: Q5.1 (G)
/IAT: M7.N15 (IAT), M11.S19 (IN_IAT)
/IAT_AT2: JP77.2 (B)
/ICV_CLOSE_LS1: JP2.2 (B)
/IDLE: M9.W38 (LOW1_DUAL), M11.E18 (OUT_PWM5)
/IDLE_LS2: D14.2 (A), JP29.2 (B)
/IGN1: M10.V8 (IGN1), M11.W1 (OUT_IGN1)
/IGN2: M10.V7 (IGN2), M11.W2 (OUT_IGN2)
/IGN3: M10.V6 (IGN3), M11.W3 (OUT_IGN3)
/IGN4: M10.V5 (IGN4), M11.W4 (OUT_IGN4)
/IGN5: M10.V4 (IGN5), M11.W5 (OUT_IGN5)
/IGN6: M10.V3 (IGN6), M11.W6 (OUT_IGN6)
/IGN7: M10.V2 (IGN7), M11.W7 (OUT_IGN7)
/IGN8: M10.V1 (IGN8), M11.W8 (OUT_IGN8)
/IGN_1: Q1.1 (G)
/IGN_2: Q2.1 (G)
/IGN_3: Q3.1 (G)
/IGN_4: Q4.1 (G)
/IGN_7: Q7.1 (G)
/IGN_8: Q8.1 (G)
/IGN_V5: M10.V9 (VCC), M11.W9 (IGN_V5)
/IGN_V33: M10.V10 (V33), M11.W10 (IGN_V33)
/INJ1: D24.2 (A), JP33.2 (B), M9.W24 (INJ1), M11.E25 (OUT_INJ1)
/INJ2: D28.2 (A), JP32.2 (B), M9.W23 (INJ2), M11.E26 (OUT_INJ2)
/INJ3: D25.2 (A), JP31.2 (B), M9.W20 (INJ3), M11.E29 (OUT_INJ3)
/INJ4: D29.2 (A), JP5.2 (B), M9.W19 (INJ4), M11.E30 (OUT_INJ4)
/INJ5: D26.2 (A), JP3.2 (B), M9.W18 (INJ5), M11.E31 (OUT_INJ5)
/INJ6: D30.2 (A), JP4.2 (B), M9.W17 (INJ6), M11.E32 (OUT_INJ6)
/INJ7: D27.2 (A), JP35.2 (B), M9.W16 (INJ7), M11.E33 (OUT_INJ7)
/INJ8: D31.2 (A), JP7.2 (B), M9.W15 (INJ8), M11.E34 (OUT_INJ8)
/INTAKE_CHRG_VLV: JP18.2 (B)
/IN_A1: M7.S25 (IN_O2S2), VIN1.1
/IN_A2: M7.S19 (IN_MAP3), VIN2.1
/IN_A3: M7.S20 (IN_AUX3), VIN3.1
/IN_A4: M7.S22 (IN_RES3), VIN4.1
/IN_AFR: M7.S9 (IN_O2S)
/IN_CAM1: M7.S5 (IN_CAM)
/IN_CAM2: M7.S21 (IN_AUX4)
/IN_CLT: M7.S15 (IN_CLT)
/IN_CRANK: M6.W2 (OUT_VR1), M7.S8 (IN_CRANK), R5.2
/IN_CRANK+: M6.E2 (IN_VR1+), R5.1
/IN_CRANK-: M6.E1 (IN_VR1-), R6.1
/IN_IAT: M7.S16 (IN_IAT)
/IN_KNOCK1: M7.S7 (IN_KNOCK), M8.E3 (OUT_KNOCK)
/IN_KNOCK1_RAW: KNOCK_RAW1.1, M8.W1 (IN_KNOCK)
/IN_KNOCK2: M7.S3 (IN_SENS3)
/IN_MAF: M7.S11 (IN_MAP1)
/IN_MAP2: M7.S12 (IN_MAP2)
/IN_PPS1: M7.S24 (IN_PPS)
/IN_PPS2: M7.S18 (IN_AUX2)
/IN_RES1: M7.S23 (IN_RES1)
/IN_RES2: M7.S26 (IN_RES2)
/IN_TPS1: M7.S10 (IN_TPS)
/IN_TPS2: M7.S17 (IN_AUX1)
/IN_VIGN: M1.V3 (IN_VIGN)
/IN_VSS: M7.S6 (IN_VSS)
/KNOCK1: M7.N22 (KNOCK), M11.S12 (IN_KNOCK)
/KNOCK2: M7.N24 (SENS3)
/KNOCK_1_3: JP70.2 (B)
/KNOCK_4_5: JP69.2 (B)
/LSU_CALIBR_RES: M3.E4 (LSU_Rtrim)
/LSU_HEAT-: M3.E5 (LSU_H+)
/LSU_PUMP_I: D13.2 (A), M3.E3 (LSU_Ip)
/LSU_SENSOR_U: M3.E1 (LSU_Un)
/LSU_SENSOR_U/PUMP_I: D10.2 (A), M3.E2 (LSU_Vm)
/MAF: M7.N14 (MAP1), M11.S20 (IN_MAP1)
/MAF_AV4: JP41.2 (B), R4.2
/MAIN: M9.W40 (LOW3_MAIN), M11.E6 (OUT_IO1)
/MAIN_RELAY: D11.2 (A), JP27.2 (B)
/MAP2: M7.N13 (MAP2), M11.S21 (IN_MAP2)
/MAP_AV1: U2.1 (VOUT)
/MIL_GP3: JP8.2 (B)
/NEUTRAL_IN_AT3: JP81.2 (B)
/NRESET: C3.1, D2.1 (K), M11.N24 (nReset), SW2.1 (A)
/OUT1: M9.W39 (LOW5_HIGH1), M11.E7 (OUT_IO2)
/OUT2: M9.W37 (LOW6_HIGH2), M11.E9 (OUT_IO4)
/OUT3: M9.W21 (LOW8), M11.E28 (OUT_PWM8)
/OUT_CE: M9.W3 (OUT_LOW4_DIODE)
/OUT_COIL_A1: M9.S1 (OUT_SOLENOID_A1)
/OUT_COIL_A2: M9.S2 (OUT_SOLENOID_A2)
/OUT_FUEL_CONSUM: M9.S6 (OUT_PP2)
/OUT_IDLE: M9.S7 (OUT_LOW1_DUAL)
/OUT_IGN1: M10.S8 (OUT_IGN1), OUT_IGN1.1
/OUT_IGN2: M10.S7 (OUT_IGN2), OUT_IGN2.1
/OUT_IGN3: M10.S6 (OUT_IGN3), OUT_IGN3.1
/OUT_IGN4: M10.S5 (OUT_IGN4), OUT_IGN4.1
/OUT_IGN5: M10.S4 (OUT_IGN5), OUT_IGN5.1
/OUT_IGN6: M10.S3 (OUT_IGN6), OUT_IGN6.1
/OUT_IGN7: M10.S2 (OUT_IGN7), OUT_IGN7.1
/OUT_IGN8: M10.S1 (OUT_IGN8), OUT_IGN8.1
/OUT_INJ1: M9.S18 (OUT_INJ1), OUT_INJ1.1
/OUT_INJ2: M9.S16 (OUT_INJ2), OUT_INJ2.1
/OUT_INJ3: M9.S17 (OUT_INJ3), OUT_INJ3.1
/OUT_INJ4: M9.W7 (OUT_INJ4), OUT_INJ4.1
/OUT_INJ5: M9.W10 (OUT_INJ5), OUT_INJ5.1
/OUT_INJ6: M9.S15 (OUT_INJ6), OUT_INJ6.1
/OUT_INJ7: M9.W12 (OUT_INJ7), OUT_INJ7.1
/OUT_INJ8: M9.W11 (OUT_INJ8), OUT_INJ8.1
/OUT_MAIN: M9.W13 (OUT_LOW3_MAIN)
/OUT_PUMP: M9.S10 (OUT_LOW10)
/OUT_TACH: M9.W6 (OUT_PP1)
/OUT_VVT1_1: M9.S13 (OUT_LOW11), M9.S14 (OUT_LOW7)
/OUT_VVT1_2: M9.W1 (OUT_LOW12), M9.W2 (OUT_LOW9)
/OUT_VVT2_B1: M9.S4 (OUT_SOLENOID_B1)
/OUT_VVT2_B2: M9.S5 (OUT_SOLENOID_B2)
/OUT_WASTEGATE: M9.W4 (OUT_LOW2_DUAL)
/PB9: J3.2 (DAT3/CD), J17.1
/PC10: J3.5 (CLK), J17.4
/PC11: J3.7 (DAT0), J17.6
/PC12: J3.3 (CMD), J17.2
/PPS1: M7.N5 (PPS), M11.S29 (IN_PPS)
/PPS2: M7.N9 (AUX2), M11.S25 (IN_AUX2)
/PUMP: D9.2 (A), M9.W35 (LOW10), M11.E8 (OUT_IO3)
/RES1: M7.N6 (RES1), M11.S28 (IN_RES1)
/RES2: M7.N3 (RES2), M11.S31 (IN_RES2)
/TACH: M9.W28 (PP1), M11.E27 (OUT_PWM7)
/TACH_GP4: JP47.2 (B)
/TPS1: M7.N17 (TPS), M11.S17 (IN_TPS)
/TPS2: M7.N10 (AUX1), M11.S24 (IN_AUX1)
/TPS_AV2: JP73.2 (B)
/USBD+: JP20.2 (B)
/USBD-: JP21.2 (B)
/USBM: J1.2 (D-), J2.2 (D-), M11.N31 (USB1M)
/USBP: J1.3 (D+), J2.3 (D+), M11.N30 (USB1P)
/V12_PERM: M1.V4 (V12_PERM)
/VBAT: M1.V2 (VBAT), M11.N17 (VBAT)
/VBUS: J1.1 (VBUS), J2.1 (VBUS), M11.N29 (VBUS)
/VIGN: M1.V5 (VIGN), M11.S7 (VIGN)
/VREF1: M7.S14 (VREF1), R6.2
/VREF2: M7.S13 (VREF2), M8.W2 (VREF)
/VSS: M7.N20 (VSS), M11.S14 (IN_VSS)
/VSS_AV3: JP42.2 (B)
/VVT1_1: M9.W27 (LOW7), M9.W36 (LOW11), M11.E10 (OUT_IO5)
/VVT1_2: M9.W26 (LOW9), M9.W29 (LOW12), M11.E21 (OUT_IO10)
/VVT2_B1: M9.W31 (SOLENOID_B1), M11.E16 (OUT_PWM3)
/VVT2_B2: M9.W30 (SOLENOID_B2), M11.E17 (OUT_PWM4)
/WASTEGATE: M9.W34 (LOW2_DUAL), M11.E12 (OUT_IO7)
/WBO2_AV6: JP13.2 (B)
GND: C3.2, D1.1 (K), J1.5 (GND), J2.5 (GND), J3.6 (VSS), J3.9 (SHIELD), J4.2, J17.5, JP6.2 (B), JP15.2 (B), JP28.2 (B), JP34.2 (B), JP39.2 (B), JP40.2 (B), JP45.2 (B), JP55.2 (B), JP84.2 (B), M1.S1 (GND), M2.E1 (GND), M3.E6 (LSU_H-), M3.G (GND), M4.E1 (GND), M5.G (GND), M6.G (GND), M7.E1 (GND), M8.E2 (GND), M9.G (GND), M9.S3 (GND), M10.G (GND), M11.S2 (GND), Q1.3 (E), Q2.3 (E), Q3.3 (E), Q4.3 (E), Q5.3 (E), Q6.3 (E), Q7.3 (E), Q8.3 (E), R3.2, R4.1, RN1.5 (R4.2), RN1.6 (R3.2), RN1.8 (R1.2), RN2.1 (R1.1), RN2.2 (R2.1), RN2.3 (R3.1), RN2.4 (R4.1), RN3.1 (R1.1), RN3.2 (R2.1), RN3.3 (R3.1), RN3.4 (R4.1), RN4.1 (R1.1), RN4.2 (R2.1), RN4.3 (R3.1), RN4.4 (R4.1), RN5.1 (R1.1), RN5.2 (R2.1), RN5.3 (R3.1), RN5.4 (R4.1), RN6.1 (R1.1), RN6.2 (R2.1), RN6.3 (R3.1), RN6.4 (R4.1), RN7.1 (R1.1), RN7.2 (R2.1), RN7.3 (R3.1), RN7.4 (R4.1), RN8.1 (R1.1), RN8.2 (R2.1), RN8.3 (R3.1), RN8.4 (R4.1), SW2.2 (B), TP4.1
GNDA: M7.J2 (PULL_GNDA), M7.J3 (PULL_RES2), M7.J4 (PULL_O2S2), M7.J6 (PULL_RES1), M7.J8 (PULL_AUX3), M7.J11 (PULL_RES3), M7.J12 (PULL_MAP3), M7.J13 (PULL_MAP2), M7.J14 (PULL_MAP1), M7.J22 (PULL_KNOCK), M7.J24 (PULL_SENS3), M7.N2 (GNDA), M11.S32 (GNDA)
unnamed: *ref1.1, JP1.1 (A)
unnamed: *ref1.2, JP2.1 (A)
unnamed: *ref1.3, JP3.1 (A)
unnamed: *ref1.4, JP4.1 (A)
unnamed: *ref1.5, JP5.1 (A)
unnamed: *ref1.6, JP6.1 (A)
unnamed: *ref1.7, JP7.1 (A)
unnamed: *ref1.8, JP8.1 (A)
unnamed: *ref1.9, JP9.1 (A)
unnamed: *ref1.10, JP10.1 (A)
unnamed: *ref1.11, JP11.1 (A)
unnamed: *ref1.12, JP12.1 (A)
unnamed: *ref1.13, JP13.1 (A)
unnamed: *ref1.14, JP14.1 (A)
unnamed: *ref1.15, JP15.1 (A)
unnamed: *ref1.16, JP16.1 (A)
unnamed: *ref1.17, JP17.1 (A)
unnamed: *ref1.18, JP18.1 (A)
unnamed: *ref1.19, JP19.1 (A)
unnamed: *ref1.20, JP20.1 (A)
unnamed: *ref1.21, JP21.1 (A)
unnamed: *ref1.22, JP22.1 (A)
unnamed: *ref1.23, JP23.1 (A)
unnamed: *ref1.24, JP24.1 (A)
unnamed: *ref1.25, JP25.1 (A)
unnamed: *ref1.26, JP26.1 (A)
unnamed: *ref1.27, JP27.1 (A)
unnamed: *ref1.28, JP28.1 (A)
unnamed: *ref1.29, JP29.1 (A)
unnamed: *ref1.30, JP30.1 (A)
unnamed: *ref1.31, JP31.1 (A)
unnamed: *ref1.32, JP32.1 (A)
unnamed: *ref1.33, JP33.1 (A)
unnamed: *ref1.34, JP34.1 (A)
unnamed: *ref1.35, JP35.1 (A)
unnamed: *ref1.36, JP36.1 (A)
unnamed: *ref1.37, JP37.1 (A)
unnamed: *ref1.38, JP38.1 (A)
unnamed: *ref1.39, JP39.1 (A)
unnamed: *ref1.40, JP40.1 (A)
unnamed: *ref1.41, JP41.1 (A)
unnamed: *ref1.42, JP42.1 (A)
unnamed: *ref1.43, JP43.1 (A)
unnamed: *ref1.44, JP44.1 (A)
unnamed: *ref1.45, JP45.1 (A)
unnamed: *ref1.46, JP46.1 (A)
unnamed: *ref1.47, JP47.1 (A)
unnamed: *ref1.48, JP48.1 (A)
unnamed: *ref1.49, JP49.1 (A)
unnamed: *ref1.50, JP50.1 (A)
unnamed: *ref1.51, JP51.1 (A)
unnamed: *ref1.52, JP52.1 (A)
unnamed: *ref1.53, JP53.1 (A)
unnamed: *ref1.54, JP54.1 (A)
unnamed: *ref1.55, JP55.1 (A)
unnamed: *ref1.56, JP56.1 (A)
unnamed: *ref1.57, JP57.1 (A)
unnamed: *ref1.58, JP58.1 (A)
unnamed: *ref1.59, JP59.1 (A)
unnamed: *ref1.60, JP60.1 (A)
unnamed: *ref1.61, JP61.1 (A)
unnamed: *ref1.62, JP62.1 (A)
unnamed: *ref1.63, JP63.1 (A)
unnamed: *ref1.64, JP64.1 (A)
unnamed: *ref1.65, JP65.1 (A)
unnamed: *ref1.66, JP66.1 (A)
unnamed: *ref1.67, JP67.1 (A)
unnamed: *ref1.68, JP68.1 (A)
unnamed: *ref1.69, JP69.1 (A)
unnamed: *ref1.70, JP70.1 (A)
unnamed: *ref1.71, JP71.1 (A)
unnamed: *ref1.72, JP72.1 (A)
unnamed: *ref1.73, JP73.1 (A)
unnamed: *ref1.74, JP74.1 (A)
unnamed: *ref1.75, JP75.1 (A)
unnamed: *ref1.76, JP76.1 (A)
unnamed: *ref1.77, JP77.1 (A)
unnamed: *ref1.78, JP78.1 (A)
unnamed: *ref1.79, JP79.1 (A)
unnamed: *ref1.80, JP80.1 (A)
unnamed: *ref1.81, JP81.1 (A)
unnamed: *ref1.82, JP82.1 (A)
unnamed: *ref1.83, JP83.1 (A)
unnamed: *ref1.84, JP84.1 (A)
unnamed: *ref1.85, JP85.1 (A)
unnamed: *ref1.86, JP86.1 (A)
unnamed: *ref1.87, JP87.1 (A)
unnamed: *ref1.88, JP88.1 (A)
unnamed: D1.2 (A), R2.2
unnamed: D2.2 (A), R1.2
unnamed: D3.1 (K), RN1.3 (R3.1)
unnamed: D4.1 (K), R3.1
unnamed: D5.1 (K), RN2.5 (R4.2)
unnamed: D6.1 (K), RN2.6 (R3.2), RN2.7 (R2.2), RN2.8 (R1.2)
unnamed: D7.1 (K), RN1.1 (R1.1)
unnamed: D8.1 (K), RN1.4 (R4.1)
unnamed: D9.1 (K), RN3.5 (R4.2)
unnamed: D10.1 (K), RN3.7 (R2.2)
unnamed: D11.1 (K), RN4.5 (R4.2)
unnamed: D12.1 (K), RN4.7 (R2.2)
unnamed: D13.1 (K), RN3.6 (R3.2)
unnamed: D14.1 (K), RN3.8 (R1.2)
unnamed: D15.1 (K), RN4.6 (R3.2)
unnamed: D16.1 (K), RN5.5 (R4.2)
unnamed: D17.1 (K), RN5.7 (R2.2)
unnamed: D18.1 (K), RN6.5 (R4.2)
unnamed: D19.1 (K), RN6.7 (R2.2)
unnamed: D20.1 (K), RN5.6 (R3.2)
unnamed: D21.1 (K), RN5.8 (R1.2)
unnamed: D22.1 (K), RN6.6 (R3.2)
unnamed: D23.1 (K), RN6.8 (R1.2)
unnamed: D24.1 (K), RN7.5 (R4.2)
unnamed: D25.1 (K), RN7.7 (R2.2)
unnamed: D26.1 (K), RN8.5 (R4.2)
unnamed: D27.1 (K), RN8.7 (R2.2)
unnamed: D28.1 (K), RN7.6 (R3.2)
unnamed: D29.1 (K), RN7.8 (R1.2)
unnamed: D30.1 (K), RN8.6 (R3.2)
unnamed: D31.1 (K), RN8.8 (R1.2)
unnamed: J14.1, M6.E3 (IN_VR2+)
unnamed: J15.1, M6.E4 (IN_VR2-)
unnamed: J16.1, M6.W1 (OUT_VR2)
unnamed: M3.W2 (CAN_VIO), M4.V2 (CAN_VIO)
unnamed: M3.W3 (CAN_RX), M4.V6 (CAN_RX)
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

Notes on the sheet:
MOSI
MISO
CLK
1 | Low side | Fuel pump 2 | Low side | ICV close 3 | Low side | Inj 5 4 | Low side | inj 6 5 | Low side | inj 4 6 | GND | gnd injectors 7 | Low side | VVT Solenoid 8 | Low side | CEL 9 | Spare | 10 | Spare | 11 | NC | Trans TPS out 12 | Analogue in | 13 | Analogue in | Lambda signal 14 | GND | MAF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
45 | GND | gnd for shield 46 | Low side | Ti signal (Fuel consumption) 47 | Low side | RPM output 48 | Low side | AC compressor relay pin 85 49 | Spare | 50 | High low | coil 1 51 | High low | coil 2 52 | High low | coil 3 53 | Spare | 54 | 12v+ | 12v from DME relay 55 | GND | gnd ignition 56 | 12v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

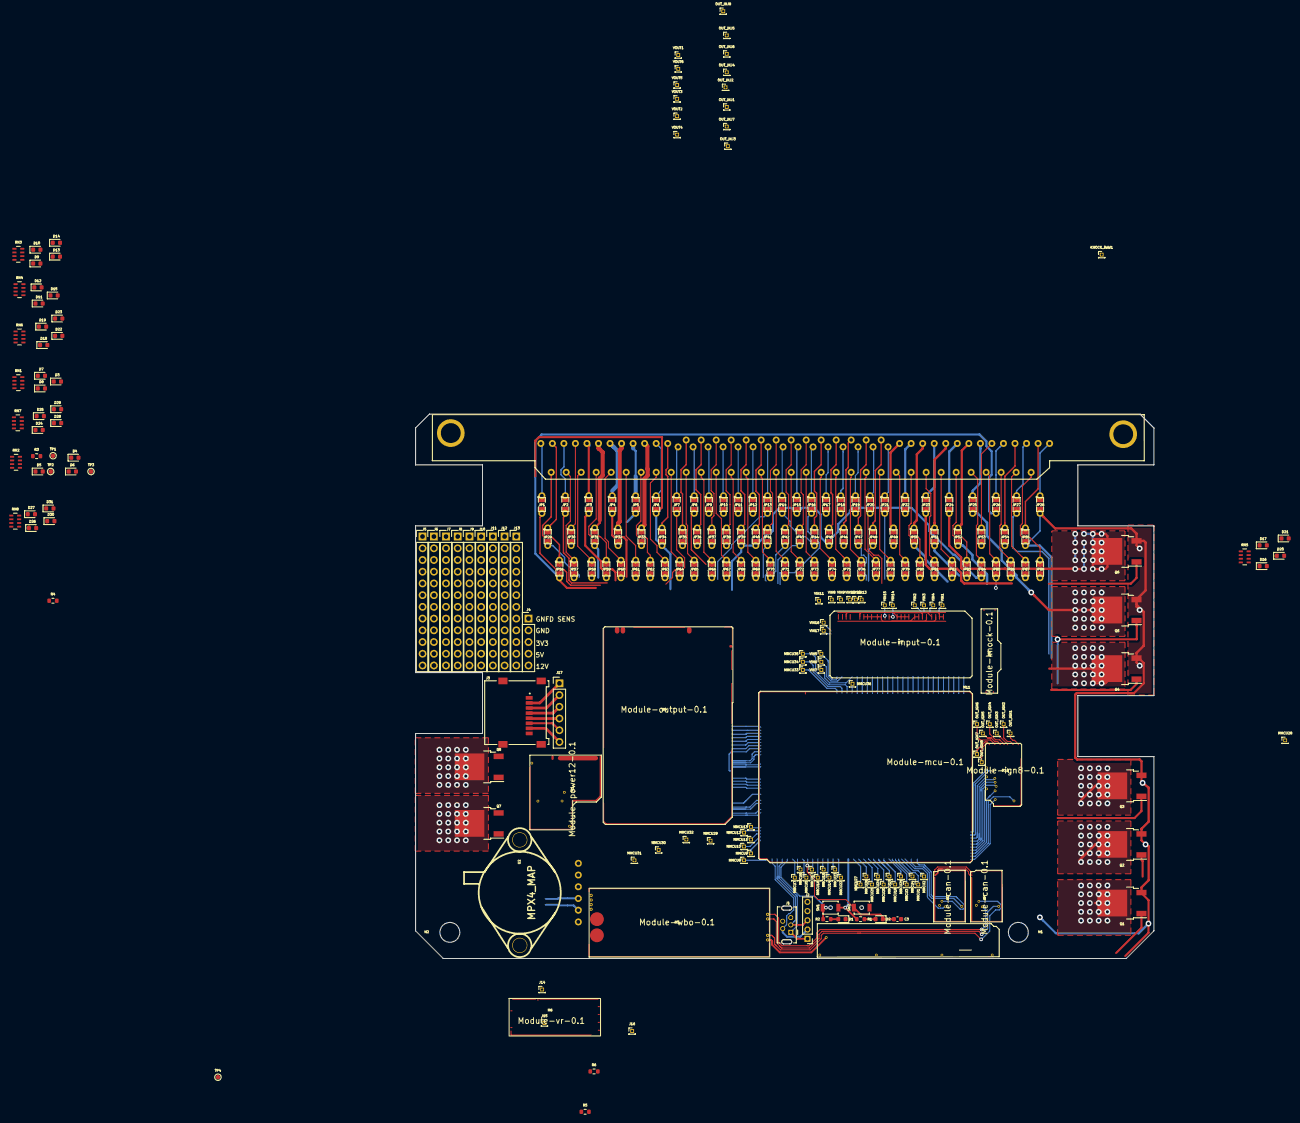
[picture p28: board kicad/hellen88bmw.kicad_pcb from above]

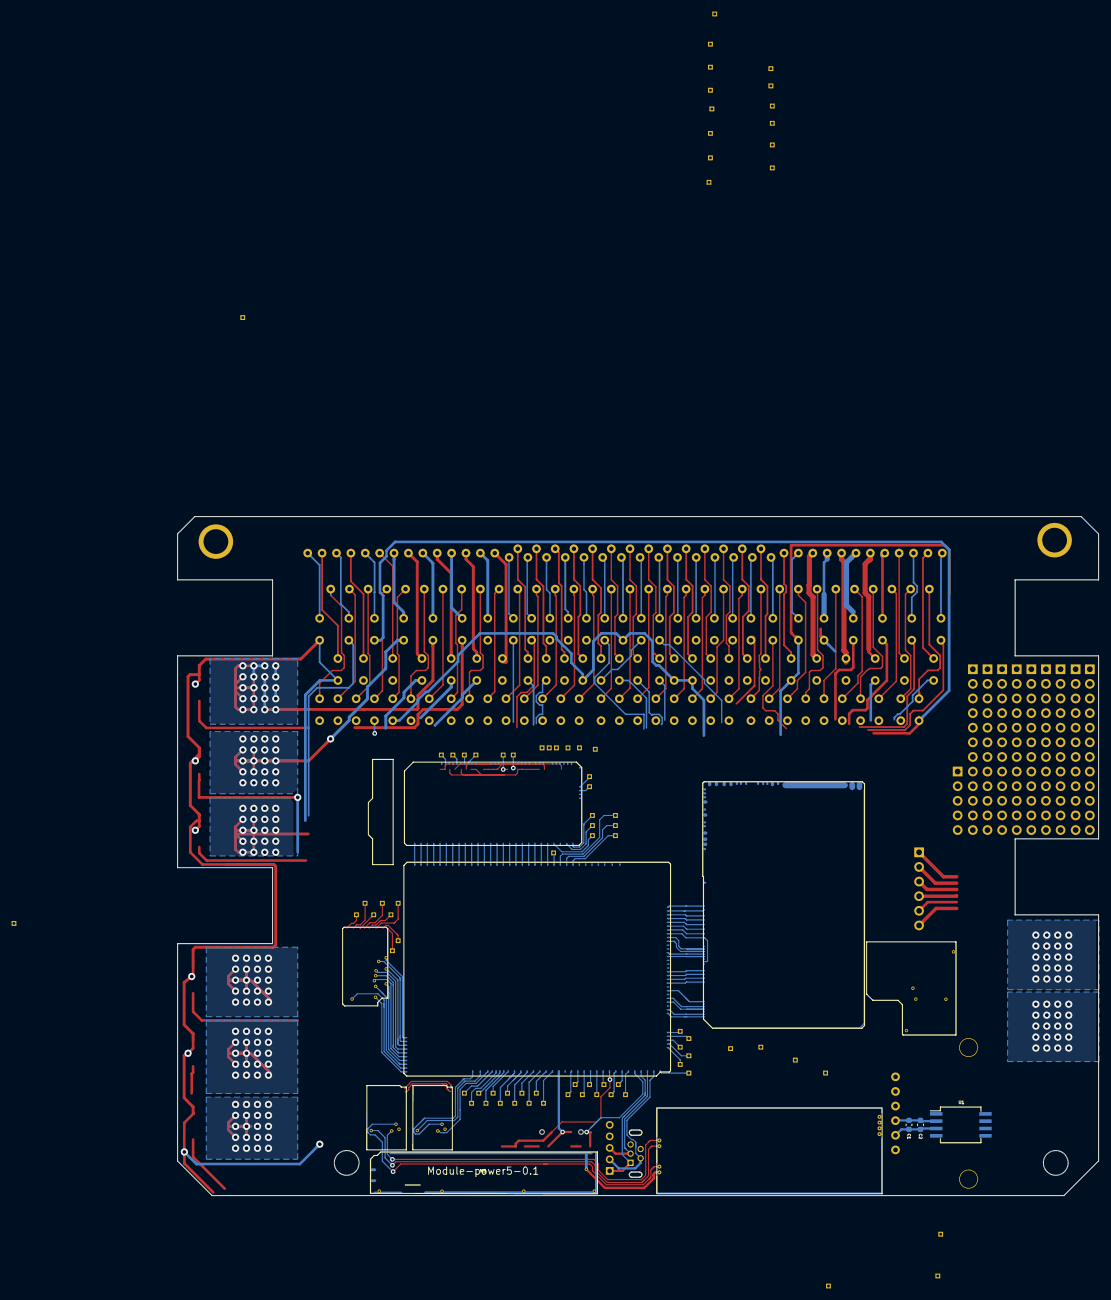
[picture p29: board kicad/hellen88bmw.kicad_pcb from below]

Board: 2 copper layers, 160.0 x 118.0 mm, 259 parts (4 on the bottom side), 302 nets.

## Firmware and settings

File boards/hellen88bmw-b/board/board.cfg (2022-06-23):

[DEFAULT]
projdir = .

[Options]
ExcellonLeadingZeros = 0
MeasurementUnits = inch
AllowMissingLayers = 1
FixedRotationOrigin = 1
PanelWidth = 19.6
PanelHeight = 15.7
[MergeOutputFiles]
Prefix = ../boards/hellen88bmw-b/board/gerber/hellen88bmw-b
*TopCopper=%(prefix)s.GTL
*TopSoldermask=%(prefix)s.GTS
*TopSolderPasteMask=%(prefix)s.GTP
*TopSilkscreen=%(prefix)s.GTO
*BottomCopper=%(prefix)s.GBL
*BottomSoldermask=%(prefix)s.GBS
*BottomSilkscreen=%(prefix)s.GBO
*Keepout=%(prefix)s.GKO
Drills=%(prefix)s.DRL
drillspth=%(prefix)s.DRL
*InnerLayer2=%(prefix)s.G1
*InnerLayer3=%(prefix)s.G2
*BottomSolderPasteMask=%(prefix)s.GBP
ToolList = %(prefix)s.tmp
Placement = %(prefix)s.tmp
BoardOutline = %(prefix)s.tmp
[88bmw]
Prefix = ../boards/hellen88bmw-b/frame/88bmw
*TopCopper=%(prefix)s.GTL
*TopSoldermask=%(prefix)s.GTS
*TopSolderPasteMask=%(prefix)s.GTP
*TopSilkscreen=%(prefix)s.GTO
*BottomCopper=%(prefix)s.GBL
*BottomSoldermask=%(prefix)s.GBS
*BottomSilkscreen=%(prefix)s.GBO
*Keepout=%(prefix)s.GKO
Drills=%(prefix)s.DRL
drillspth=%(prefix)s.DRL
*InnerLayer2=%(prefix)s.G1
*InnerLayer3=%(prefix)s.G2
BoardOutline=%(prefix)s.GM15
[power12]
Prefix = modules/power12/0.2/power12
*TopCopper=%(prefix)s.GTL
*TopSoldermask=%(prefix)s.GTS
*TopSolderPasteMask=%(prefix)s.GTP
*TopSilkscreen=%(prefix)s.GTO
*BottomCopper=%(prefix)s.GBL
*BottomSoldermask=%(prefix)s.GBS
*BottomSilkscreen=%(prefix)s.GBO
*Keepout=%(prefix)s.GKO
Drills=%(prefix)s.DRL
drillspth=%(prefix)s.DRL
BoardOutline=%(prefix)s.GM15
[can]
Prefix = modules/can/0.1/can
*TopCopper=%(prefix)s.GTL
*TopSoldermask=%(prefix)s.GTS
*TopSolderPasteMask=%(prefix)s.GTP
*TopSilkscreen=%(prefix)s.GTO
*BottomCopper=%(prefix)s.GBL
*BottomSoldermask=%(prefix)s.GBS
*BottomSilkscreen=%(prefix)s.GBO
*Keepout=%(prefix)s.GKO
Drills=%(prefix)s.DRL
drillspth=%(prefix)s.DRL
BoardOutline=%(prefix)s.GM15
[wbo]
Prefix = modules/wbo/0.3/wbo
*TopCopper=%(prefix)s.GTL
*TopSoldermask=%(prefix)s.GTS
*TopSolderPasteMask=%(prefix)s.GTP
*TopSilkscreen=%(prefix)s.GTO
*BottomCopper=%(prefix)s.GBL
*BottomSoldermask=%(prefix)s.GBS
*BottomSilkscreen=%(prefix)s.GBO
*Keepout=%(prefix)s.GKO
Drills=%(prefix)s.DRL
drillspth=%(prefix)s.DRL
BoardOutline=%(prefix)s.GM15
[can_2]
Prefix = modules/can/0.1/can
*TopCopper=%(prefix)s.GTL
*TopSoldermask=%(prefix)s.GTS
*TopSolderPasteMask=%(prefix)s.GTP
*TopSilkscreen=%(prefix)s.GTO
*BottomCopper=%(prefix)s.GBL
*BottomSoldermask=%(prefix)s.GBS
*BottomSilkscreen=%(prefix)s.GBO
*Keepout=%(prefix)s.GKO
Drills=%(prefix)s.DRL
drillspth=%(prefix)s.DRL
BoardOutline=%(prefix)s.GM15
[power5]
Prefix = modules/power5/0.2/power5
*TopCopper=%(prefix)s.GTL
*TopSoldermask=%(prefix)s.GTS
*TopSolderPasteMask=%(prefix)s.GTP
*TopSilkscreen=%(prefix)s.GTO
*BottomCopper=%(prefix)s.GBL
*BottomSoldermask=%(prefix)s.GBS
*BottomSilkscreen=%(prefix)s.GBO
*Keepout=%(prefix)s.GKO
Drills=%(prefix)s.DRL
drillspth=%(prefix)s.DRL
BoardOutline=%(prefix)s.GM15
[vr]
Prefix = modules/vr/0.1/vr
*TopCopper=%(prefix)s.GTL
*TopSoldermask=%(prefix)s.GTS
*TopSolderPasteMask=%(prefix)s.GTP
*TopSilkscreen=%(prefix)s.GTO
*BottomCopper=%(prefix)s.GBL
*BottomSoldermask=%(prefix)s.GBS
*BottomSilkscreen=%(prefix)s.GBO
*Keepout=%(prefix)s.GKO
Drills=%(prefix)s.DRL
drillspth=%(prefix)s.DRL
BoardOutline=%(prefix)s.GM15
[input]
Prefix = modules/input/0.1/input
*TopCopper=%(prefix)s.GTL
*TopSoldermask=%(prefix)s.GTS
*TopSolderPasteMask=%(prefix)s.GTP
*TopSilkscreen=%(prefix)s.GTO
*BottomCopper=%(prefix)s.GBL
*BottomSoldermask=%(prefix)s.GBS
*BottomSilkscreen=%(prefix)s.GBO
*Keepout=%(prefix)s.GKO
Drills=%(prefix)s.DRL
drillspth=%(prefix)s.DRL
BoardOutline=%(prefix)s.GM15
[knock]
Prefix = modules/knock/0.1/knock
*TopCopper=%(prefix)s.GTL
*TopSoldermask=%(prefix)s.GTS
*TopSolderPasteMask=%(prefix)s.GTP
*TopSilkscreen=%(prefix)s.GTO
*BottomCopper=%(prefix)s.GBL
*BottomSoldermask=%(prefix)s.GBS
*BottomSilkscreen=%(prefix)s.GBO
*Keepout=%(prefix)s.GKO
Drills=%(prefix)s.DRL
drillspth=%(prefix)s.DRL
BoardOutline=%(prefix)s.GM15
[output]
Prefix = modules/output/0.3/output
*TopCopper=%(prefix)s.GTL
*TopSoldermask=%(prefix)s.GTS
*TopSolderPasteMask=%(prefix)s.GTP
*TopSilkscreen=%(prefix)s.GTO
*BottomCopper=%(prefix)s.GBL
*BottomSoldermask=%(prefix)s.GBS
*BottomSilkscreen=%(prefix)s.GBO
*Keepout=%(prefix)s.GKO
Drills=%(prefix)s.DRL
drillspth=%(prefix)s.DRL
BoardOutline=%(prefix)s.GM15
[ign8]
Prefix = modules/ign8/0.2/ign8
*TopCopper=%(prefix)s.GTL
*TopSoldermask=%(prefix)s.GTS
*TopSolderPasteMask=%(prefix)s.GTP
*TopSilkscreen=%(prefix)s.GTO
*BottomCopper=%(prefix)s.GBL
*BottomSoldermask=%(prefix)s.GBS
*BottomSilkscreen=%(prefix)s.GBO
*Keepout=%(prefix)s.GKO
Drills=%(prefix)s.DRL
drillspth=%(prefix)s.DRL
BoardOutline=%(prefix)s.GM15
[mcu144]
Prefix = modules/mcu144/0.6/mcu144
*TopCopper=%(prefix)s.GTL
*TopSoldermask=%(prefix)s.GTS
*TopSolderPasteMask=%(prefix)s.GTP
*TopSilkscreen=%(prefix)s.GTO
*BottomCopper=%(prefix)s.GBL
*BottomSoldermask=%(prefix)s.GBS
*BottomSilkscreen=%(prefix)s.GBO
*Keepout=%(prefix)s.GKO
Drills=%(prefix)s.DRL
drillspth=%(prefix)s.DRL
BoardOutline=%(prefix)s.GM15
[knock_2]
Prefix = modules/knock/0.1/knock
*TopCopper=%(prefix)s.GTL
*TopSoldermask=%(prefix)s.GTS
*TopSolderPasteMask=%(prefix)s.GTP
*TopSilkscreen=%(prefix)s.GTO
*BottomCopper=%(prefix)s.GBL
*BottomSoldermask=%(prefix)s.GBS
*BottomSilkscreen=%(prefix)s.GBO
*Keepout=%(prefix)s.GKO
Drills=%(prefix)s.DRL
drillspth=%(prefix)s.DRL
BoardOutline=%(prefix)s.GM15
[sd]
Prefix = modules/sd/0.1/sd
*BottomCopper=%(prefix)s.GTL
*BottomSoldermask=%(prefix)s.GTS
*BottomSolderPasteMask=%(prefix)s.GTP
*BottomSilkscreen=%(prefix)s.GTO
*TopCopper=%(prefix)s.GBL
*TopSoldermask=%(prefix)s.GBS
*TopSilkscreen=%(prefix)s.GBO
*Keepout=%(prefix)s.GKO
Drills=%(prefix)s.DRL
drillspth=%(prefix)s.DRL
BoardOutline=%(prefix)s.GM15

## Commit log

2021-01-27 frame starting point
    [88pin.kicad_pcb]
2021-03-18 Up hellen88
    [88pin.kicad_pcb, hellen88bmw.kicad_pcb, hellen88bmw.kicad_sch]
2021-03-21 Up 88bmw update
    [hellen88bmw.kicad_sch]
2021-04-01 Up 88 update
    [hellen88bmw.kicad_sch]
2021-04-26 Up 88
    [hellen88bmw.kicad_pcb, hellen88bmw.kicad_sch]
2021-07-02 Up hellen88bmw
    [hellen88bmw.kicad_pcb, hellen88bmw.kicad_sch]
2021-07-05 Up hellen88bmw 5.07.2021
    [hellen88bmw.kicad_pcb, hellen88bmw.kicad_sch]
2021-07-06 Up hellen88bmw 6.07.2021
    [hellen88bmw.kicad_pcb, hellen88bmw.kicad_sch]
2021-07-14 Up issue 26.28.29
    [hellen88bmw.kicad_pcb, hellen88bmw.kicad_sch]
2021-07-14 Up issue 30
    [hellen88bmw-B_Cu.gbl, hellen88bmw-B_Mask.gbs, hellen88bmw-B_Paste.gbp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]
2021-07-14 hellen-one scripts
    [bom_replace_88bmw-a.csv]
2021-07-21 Up 20/072021
    [hellen88bmw.csv, hellen88bmw.kicad_pcb, hellen88bmw.kicad_sch]
2021-07-22 Up 21/072021
    [hellen88bmw.kicad_pcb, hellen88bmw.kicad_sch]
2021-08-03 Up 04/082021
    [88bmw-BOM.csv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]
2021-08-12 Up 12/08/2021
    [board.cfg, hellen88bmw-a-BOM.csv, hellen88bmw.csv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]
2021-08-12 Up 12/08/2021 part 2
    [hellen88bmw-B_Cu.gbl, hellen88bmw-B_Mask.gbs, hellen88bmw-B_Paste.gbp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]
2021-08-14 fix 14/08/2021
    [88bmw-BOM.csv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]
2021-08-14 fix 2 14/08/2021
    [88bmw-BOM.csv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]
2021-08-16 16/08/2021 fix 1
    [88bmw-CPL.csv, 88bmw.DRL, 88bmw.GBL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]
2021-08-16 BOM issues #45
    [bom_replace_88bmw-a.csv]
2021-08-16 BOM fix
    [88bmw-BOM.csv, hellen88bmw-a-BOM.csv, hellen88bmw.csv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]
2021-08-17 BOM fix 17/08/2021
    [88bmw-BOM.csv, hellen88bmw-a-BOM.csv, hellen88bmw.csv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]
2021-08-17 fix schematic and board
    [88bmw-BOM.csv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]
2021-08-23 Issues 61,60,59,57,55,54,17,6,13,8,16,12
    [hellen88bmw.kicad_sch]
2021-08-28 update 28/08/2021
    [hellen88bmw.kicad_pcb, hellen88bmw.kicad_sch]
2021-08-30 update 29/08/2021
    [hellen88bmw.kicad_sch]
2021-08-31 update 31/08/2021
    [hellen88bmw.kicad_sch]
2021-08-31 lib update 31/08/2021 2
    [hellen88bmw.kicad_sch]
2021-09-03 pcb board
    [88bmw-BOM.csv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]
2021-09-04 ETB tracer fix
    [88bmw-CPL.csv, 88bmw.DRL, 88bmw.GBL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]
2021-09-15 Sch refactoring
    [hellen88bmw.kicad_sch]
2021-09-16 PCB refactoring started
    [hellen88bmw.kicad_sch]
2021-09-18 Upd pcb
    [hellen88bmw.kicad_sch]
2021-09-21 DRC fix, test export
    [88bmw-BOM.csv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]
2021-09-21 Export preview
    Problem with SD module on bottom
    [88bmw.DRL, 88bmw.GBL, 88bmw.GBO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]
2021-09-28 Wbo 0.3
    [88bmw-CPL.csv, hellen88bmw-a-CPL.csv, hellen88bmw-a.DRL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]
2021-10-02 Double side preview
    [88bmw-BOM.csv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]
2021-10-02 Fresh export. JLC adjustments
    [88bmw-BOM.csv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]
2021-10-04 VIGN fix
    [hellen88bmw.kicad_sch]
2021-10-05 Fresh fab exprot
    [88bmw.DRL, 88bmw.GBL, 88bmw.GBO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]
2021-10-06 DRL fix
    [hellen88bmw-a.DRL]
2022-06-21 Some fixes
    #34, #46, #43, #45, #23, #33, #28, #3, #27, #49, #48, #47, #44, #26
    [88bmw-BOM.csv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]
2022-06-21 Rename replace
    [bom_replace_hellen88bmw-b.csv]
2022-06-21 Auto-generated board
    [board.cfg]
2022-06-21 Upd replace
    [bom_replace_hellen88bmw-b.csv]
2022-06-23 Fab export
    [88bmw-BOM.csv, board.cfg, hellen88bmw-b-BOM.csv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]
2022-09-21 [skip actions] Auto-generated board
    [88bmw-BOM.csv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]
2023-03-16 remove kicad-libraries-private
2023-06-02 Use scripts in workflow and install kicad
2023-06-03 install kicad-netlist-reader
